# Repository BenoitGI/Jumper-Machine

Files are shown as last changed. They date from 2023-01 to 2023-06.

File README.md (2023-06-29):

 <h1> Jumper Machine 2022/2023 </h1>

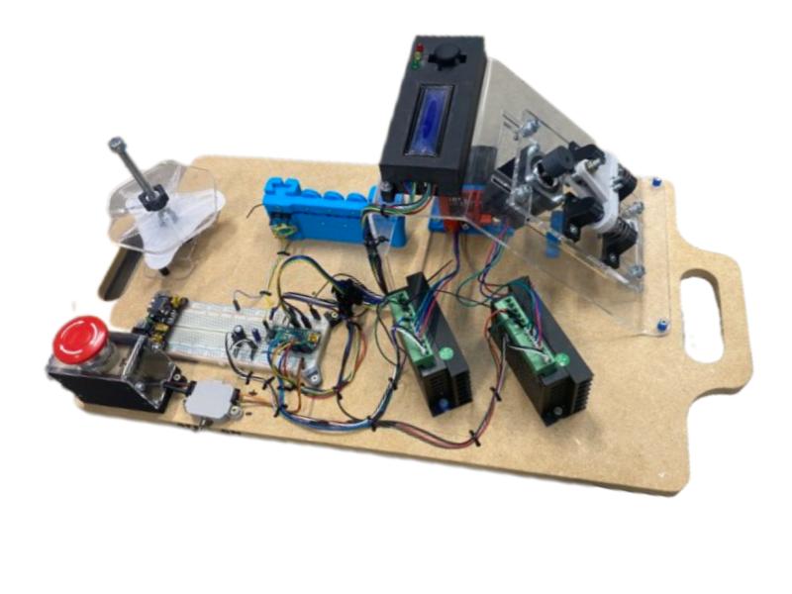
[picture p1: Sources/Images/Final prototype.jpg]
Jumper Machine final prototype


## Introduction
This OnShape project is a part of an french engineering school project (**Grenoble INP - Génie Industriel**) realized during 2022/2023. During 1 year, our group of 5 students had to make a machine prototype which would automatize the manufacturing of connecting wire for prototyping  named “jumper” from a wire reel. It was ordered by the **Ense3 Favlab** and realized on the **Smart Platform**.

We also own an OnShape file with all our CAD models and assemblies 
<center>

**[<span font-size:7em> Project's Onshape Link </span>](https://cad.onshape.com/documents/e23f2a9b7d5cbfc350862d24/w/3bd71b5e537bce5bc2623e5e/e/d0d5c7eefa7db94f148151a4)**

</center>

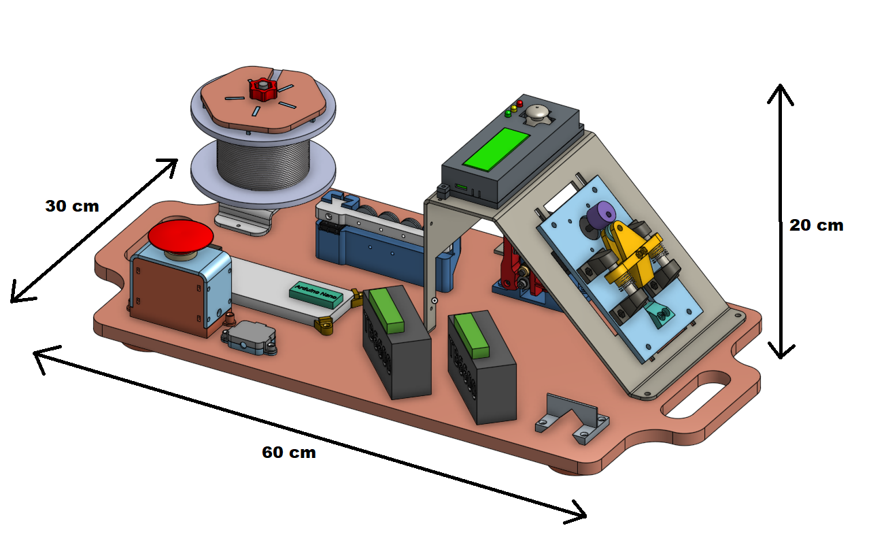
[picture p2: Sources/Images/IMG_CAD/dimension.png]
3D view with dimensions


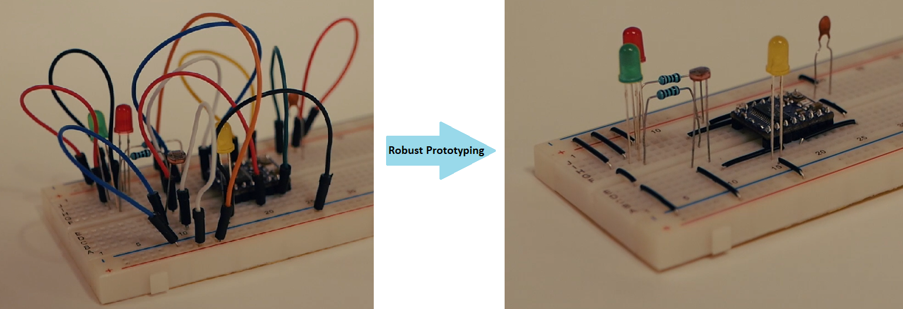
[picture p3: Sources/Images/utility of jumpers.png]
Utility of jumpers in prototyping


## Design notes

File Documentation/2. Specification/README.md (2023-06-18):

# **Specifications**

In order to best meet the customer's needs, we felt it was more efficient to ask him directly what he wanted from our machine. To do this, we drew up a first set of specifications and sent them to him. This was followed by several email exchanges and corrections to the specifications. We were also able to prioritize the functions of the machine from the most important to the least important with the customer. We also integrated a method of verification for each function (visual method, on software, by measurement, etc). To date, here are our main objectives.

## **Main objectives of this project**
<details>
  <summary>Jumper machine : objectives and constraints</summary>

First of all, the machine must distribute rigid wire. It must therefore be fed with wire, tension the wire and make it circulate in the system. The tensioned wire must not deviate from its initial axis by more than 1 millimeter.

Then, the machine must cut the wire to the right length and in bizot (45 degree angle). The length of wire to be cut ranges from 5.08 to 50.8 mm with a pitch of 2.54 mm with a tolerance of 0.5 mm.

As for the removal of the sleeve, it must be done on the left and right parts of the cut wire on a length of 6.5 mm on each side with a tolerance of 0.5 mm. This step must be done with care in order not to damage the conductors. We have also thought of a sorting system in order to differentiate between the waste of the sleeve and the waste of the conductor wire.

For the bending part of the machine, the edges of the wires must be bent at 90° with a tolerance of 5°, and above all they must not modify the initial geometry of the wire, that is to say that the wire must remain straight.

Then, for the operation of the machine, the customer would like it to be powered by different sources (nomadic mode, 12v DC) and to withstand the temperature conditions of a laboratory. Moreover, the machine must also respect a rate of 1 jumper in 10 seconds. It must be reliable, i.e. it must produce at least 10 jumpers in a row that comply with the specifications mentioned above. But the machine must also be dismountable and mountable with simple tools in one hour maximum.

As far as safety is concerned, the customer would like the machine to stop completely in less than one second with a simple manipulation. Also, if the instructions are not followed, the machine should not start. Moreover, during its operation no moving part of the system should be reachable by the user.

Finally, for the spatial dimensions, the system must not exceed the dimensions L50*W30*H30 cm and must not weigh more than 15 Kg.
 </details>
 
## **State of the art**
<details>
  <summary>Cutting, stripping and dispensing wire</summary>

Since a few decades, human beings have been using wires, especially jumpers, for electronic systems and often need to cut and strip them. That’s why they have created both wire cutter and wire stipper, then he wanted to do both those tasks with only one tool. Today, there are machines which can automatically cut and strip wires. They can either be big industrial machines or homemade ones depending on making rate, quantity, … It’s also possible for some machines to bend wires in order to make jumpers.

Using wire stipper or special blades can be considered as the main way to get stripped wires even though a carbon-dioxide laser is a good solution as well. However, a carbon-dioxide laser is very expensive thus outside the budget. The last solution to strip a wire we thought about consisted in using chemicals to dissolve the wire sleeve but we have quickly forgotten this solution because of its dangerousness.

About bending, there are many existing solutions and not only the basic one by using a plier but also, for example, an interesting and uncommon way with a hot wire. On the Internet, most bending machines work with a spinning part (linked to a stepper) and an offset axis.
			
A wire cutting machine “typically feeds the wire in on a reel, marks the wire using an inkjet or hot stamp printing mechanism, cuts the wire, and then coils the finished product on another reel or stacks it in a guide channel” [2].
A wire cutting/stripping machine usually has a rotating blade that follows the input cable and strips or cuts away the insulation.
However, such tools are expensive, and can’t be afforded by small workshops. For example, the Model WS-212 wire stripping machine by Bluerock Tools costs $ 1,299.00. Moreover the machine weighs 90 kilograms which is not convenient to be carried. The main issue with old wire cutting machines is the fact that they are not accurate or reliable. They tend to waste material which is an important issue when you are doing a project for the school of the environment.

Before the appearance of the first machines for cutting and stripping electrical wires, these tasks had to be done manually. Thanks to the particular shape of its blades, the "classic" cutting pliers can easily cut wires of various diameters.

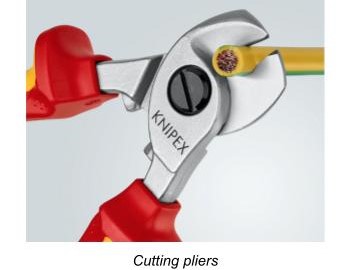
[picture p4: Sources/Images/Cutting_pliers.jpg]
Cutting pliers


For the stripping pliers, there are more or less sophisticated models. A calibrated wire stripper is very interesting for stripping small diameter wires, but its range of action is limited by its size. Indeed, the more it is possible to use it for different wires, the more it will be cumbersome. For this reason, it is sometimes interesting to have a second stripper at one's disposal to strip wires with a larger diameter.

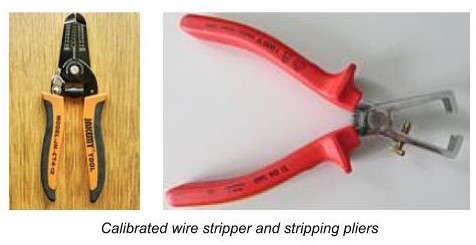
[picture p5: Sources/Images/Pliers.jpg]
Pliers


Stripping a wire is based on the principle of two blades that partially cut a sleeve that surrounds the electrical wires. Then pull to detach a piece of the sleeve. However, it may be interesting to be inspired by the principle of a foil cutter. That is to say, to have a device equipped with four rotating circular blades that can cut the sleeve around the wires completely.

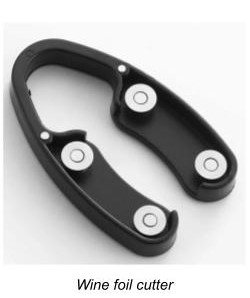
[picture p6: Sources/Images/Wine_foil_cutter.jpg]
Wine foil cutter


The use of blades to cut and strip wires is certainly the most common because of its simplicity, its low risk of injury but especially its very low cost compared to other devices. 

It is possible to perform these cutting and stripping tasks automatically with machines made by professionals [3] and usually sold at high prices. However, many individuals wish to have such machines to make their own jumpers. That's why there are DIY machines [4] with tutorials available online so you can make them yourself. All of these machines work in much the same way. The wire first passes through a tensioning system which also allows to straighten it. It’s then pulled by rollers which, according to their direction of rotation, make the wire advance or retreat. Finally, these machines use two V-shaped blades capable of cutting and stripping the wire. The whole thing is often managed by an Arduino type board that controls stepper motors. Finally, the use of such machines allows to cut and strip wires much faster than with pliers. It is especially possible to manufacture some of them for a lower cost.

V-blade technology is not the only technology that can be used for wire stripping. In fact, some individuals have already built their own machines and used a laser to strip the wires.

You might wonder why should a laser be considered for this purpose when the equipment is significantly more expensive than the competing methods?
The answer lies in its easy integration with electromechanical equipment, high controllability, non-contact process and no cutting force on the workpiece. Previous researches have proved that laser means has absolute advantages over traditional ways of mechanical wire stripping. [5]

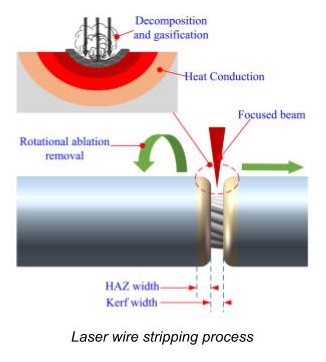
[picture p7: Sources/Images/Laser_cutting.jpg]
Laser stripping


Currently, carbon dioxide lasers are used on stripping machines because of their ability to selectively remove only the insulation without damaging the wire.
The absorption coefficient of non-metal material for this kind of laser wavelength is high and the absorption coefficient of metal material for this kind of laser wavelength is low, so the metal layer will not be damaged.
Laser wire stripping has been effectively applied as a production process in the aerospace, medical and data communications fields. There are specific advantages of using a laser over other methods but the emphasis varies from application to application.

Advantages : 
Selectively removes insulation with no conductor damage.
Near perfect process yield.
Lowest rework costs.
Provides excellent wire integrity, significantly increasing product life and reliability.
Can be automated, reducing labor costs.

Lasers have become valuable tools in manufacturing. Laser wire stripping is now performing production requirements very satisfactorily. The companies requiring wire stripping can now use lasers for this purpose and have various processes that cover all insulation materials presently in use.

Drawbacks :
High component costs.
If not fully automated, need for protection for users (closed carter and protective eyewear).
Need for a ventilation system to avoid accumulation of toxic fumes.

In the 2000s, NASA developed a manufacturing standard for wire stripping using chemical agents [6] . This method can only be used for single-conductor wires, but it is effective and allows a clean stripping without sleeve residues. However, the use of such chemical agents remains dangerous even if it seems to be possible to buy professional chemical pots [7] that enable the user to strip wires by using the method with chemical agents.

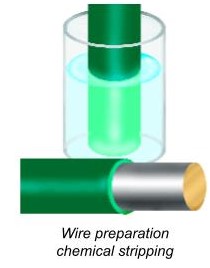
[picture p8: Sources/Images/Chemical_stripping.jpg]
Chemical stripping


In order to bend the wires in the least complex way possible, one would simply use pliers to bend the stripped ends into the desired jumper shape. The disadvantage of this method is that it is not very fast, it can be a pain for smaller wires and it does not allow a good regularity of the jumper shape. On the other hand, it is possible to consider 3D printing a bending die allowing to deposit the wires according to the corresponding size, then to press on the edges in order to bend them. This method could also be semi-automated or even totally automated by considering two dies (female and male) that would perform the bending and would overcome some of the shortcomings of the entirely manual method.

The most commonly used solution for bending wires is to use a part controlled by a stepper motor and equipped with an eccentric and extruded cylinder. There are many machines with different designs. Indeed, some are arranged horizontally [8] and others vertically [9] . It does not seem that either of these operating modes offers any particular advantages. The majority of the machines only allow folding. However, there are some machines that are able to perform all three tasks at once [10] .

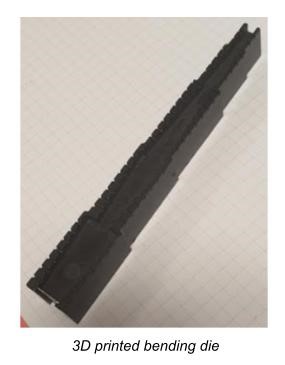
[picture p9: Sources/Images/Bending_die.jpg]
Bending die


The last possible method is probably one of the least used, but it is quite possible to bend wires using an electrically heated wire [11] . It works in much the same way as the bending die, but the effort required to bend the wire is reduced. The main disadvantage of this technique is obviously the risk of burning.

[2] Wire Cutting Machines Information, para. 1, Globalspec, accessed 06/10/2022, website, https://www.globalspec.com/learnmore/manufacturing_process_equipment/machine_tools/wire_cutting_machi nes 
[3]Eraser’s catalog, p.15-29, accessed 06/11/2022, pdf document, https://www.eraser.com/pdf/Eraser_Catalog.pdf
[4] Wire cutter stripper machine DIY, Ivan Rodyk, accessed 06/11/2022, Youtube video, https://www.youtube.com/watch?v=mNCjpKPapnc&ab_channel=IvanRodyk
[5] Study on the optimal process parameters for stripping the X-ETFE insulation layer of aviation wires by a small semiconductor laser, Sage Journals, accessed 10/10/2022, Research Article, https://doi.org/10.1177/16878132221127592
[6] Wire Preparation Chemical Stripping, Nasa Workmanship Standard, accessed 06/11/2022, Research Article, https://workmanship.nasa.gov/lib/insp/2%20books/links/sections/104%20Chemical%20Stripping.html
[7] Chemical Wire Stripping, Eraser, accessed 06/11/2022, Website, https://www.eraser.com/products/wire-cable-strippers/chemical-wire-stripping/
[8] DIY Wire Bender ets wires all bend into shape, Steven Dufresne, Hackaday, accessed 06/11/2022, Blog, https://hackaday.com/2018/10/14/diy-wire-bender-gets-wires-all-bent-into-shape/
[9] Arduino wire bender probably won’t kill all humans, Kristina Panos, Hackaday, accessed 06/11/2022, Blog, https://hackaday.com/2019/09/28/arduino-wire-bender-probably-wont-kill-all-humans/
[10] Fully Automatic Wire Cutter Stripper Bender Machine YH-680Z, Kunshan Yuanhan Electronic Equipment, accessed 06/11/2022, Youtube video, https://www.youtube.com/watch?v=nUAdrEDehpE&ab_channel=KunshanYuanhanElectronicEquipment
[11] Bending materials with a simple hot wire forming tool, Mike Szczys, Hackaday, accessed 06/11/2022, Blog, https://hackaday.com/2013/02/28/bending-materials-with-a-simple-hot-wire-forming-tool/
 </details>
	
## **Stakeholders**
<details>
  <summary>Stakeholders</summary>
	
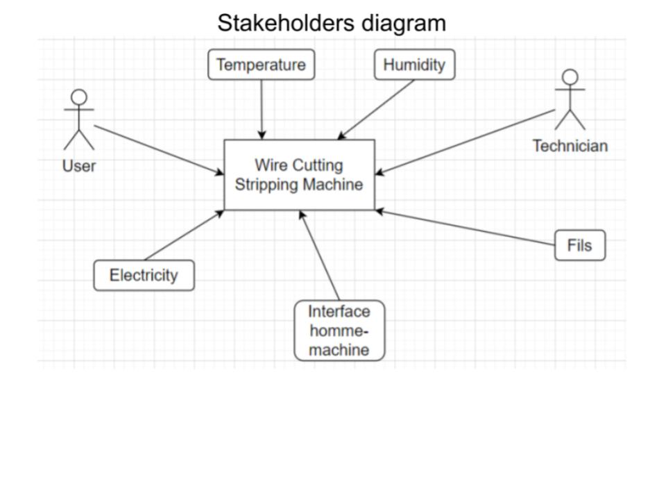
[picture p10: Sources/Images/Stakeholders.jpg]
Stakeholders of the jumper machine

	
 </details>

## **Requirement**

<details>
  <summary>Specifications</summary>

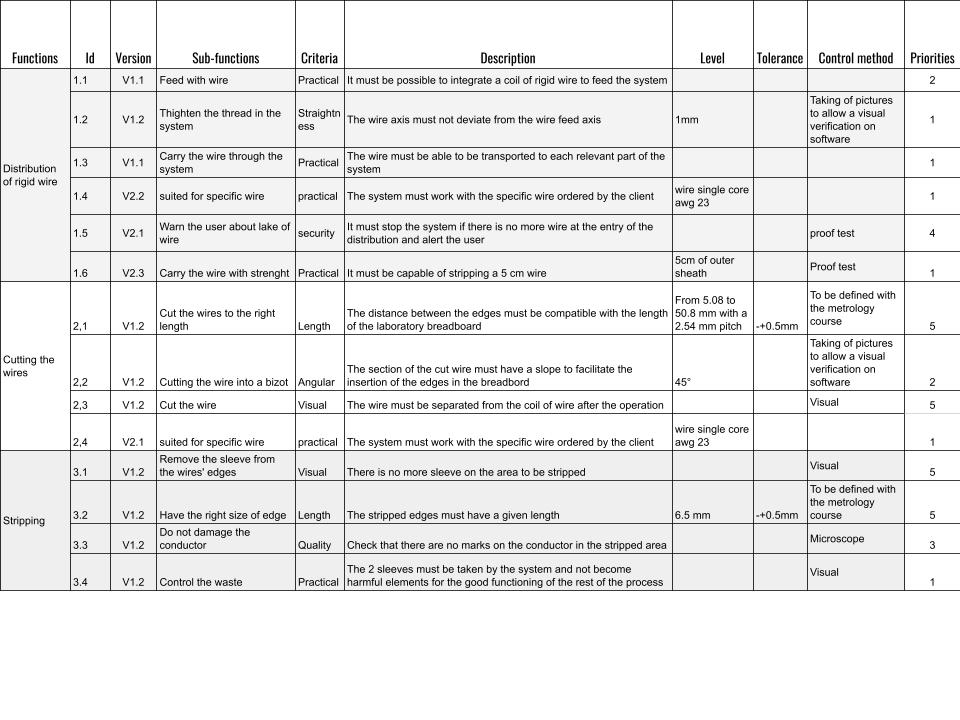
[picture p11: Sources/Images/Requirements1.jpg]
Requirements part 1

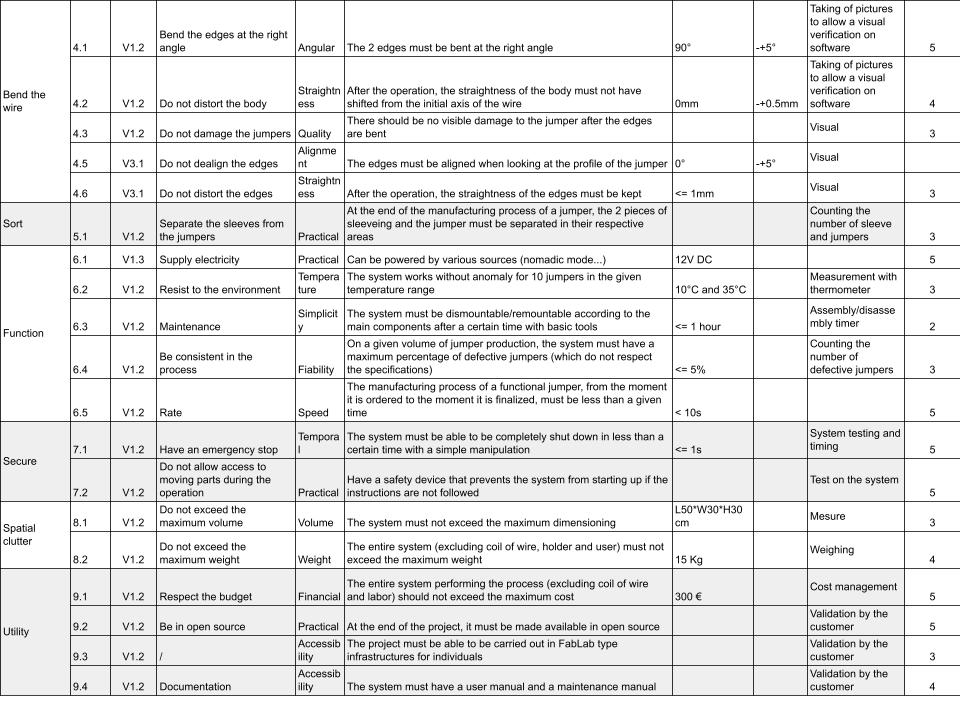
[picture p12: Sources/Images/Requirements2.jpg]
Requirements part 2


 </details>
 
## **Workplan**
<details>
  <summary>Project managment</summary>

  From the beginning of the project, we had in mind to share the work between us by "Functional Block" of the project (cut, strip, fold, feed) to allow us to advance in parallel and thus to be more efficient. Moreover, our objective was to get as close as possible to the customer's expectations by regularly exchanging with him on our progress or our questions.
That's why the AGILE method seemed to be adapted in our case.

We are going to apply it by separating ourselves into two groups (2 and 3 people) who will each take care of one of the functional blocks during a design cycle and which will then be concluded by a customer feedback. Once this feedback is done, we start a new design cycle, either to make adjustments or to start a new functional block.
Moreover, this method offers us the advantage of being quite flexible because if we are short of time, we can decide to "amputate" the system of certain functions (the priorities having been defined with the customer).

As things stand now, and taking into account that we don't only have the PDP in our schedule. We hope to complete at least 2 cycles before we reach the phase where we will integrate all our functional blocks into the complete system (assembly phase).

Agile cycle

Our goal is to send at least one email to the client every 2 weeks to allow him to be involved in our progress. 
For now, we have done all the preparatory phase to be able to divide the work and understand the ins and outs of the project. Now, we will split up and start the first Agile cycle in anticipation of a meeting with the client just before the Christmas vacations.

With regard to document management, we have a drive because the project is not subject to industrial confidentiality. And we have decided on a title nomenclature as follows:

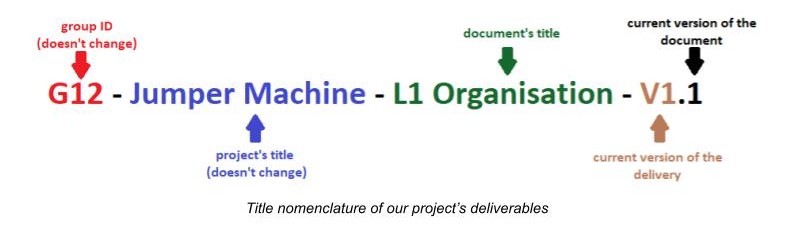
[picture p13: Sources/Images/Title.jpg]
Documents nomenclature
	

Nevertheless, we make sure that the latest version of a document is on chamilo.

</details>

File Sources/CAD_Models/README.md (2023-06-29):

You will find here all the **CAD models** used to build the Jumper Machine. 
we remind you that we have an OnShape repository (if you have a licence)  where their are all our CAD models and assemblies : 

[Jumper Machine 2022/2023](https://cad.onshape.com/documents/e23f2a9b7d5cbfc350862d24/w/3bd71b5e537bce5bc2623e5e/e/d0d5c7eefa7db94f148151a4)

For each of our part on this GitHub project,  you'll have :
- **.STL** if you just want to print the part.
- **.Dxf** if it's a part make by a laser cutting technologie.
- **.pdf** for bending plans for certain parts
- **.FCStd** which allow you to modify the part on a free and open-source CAD software named [**FreeCAD**](https://www.freecad.org/index.php).

# Jumper Machine Nomenclature
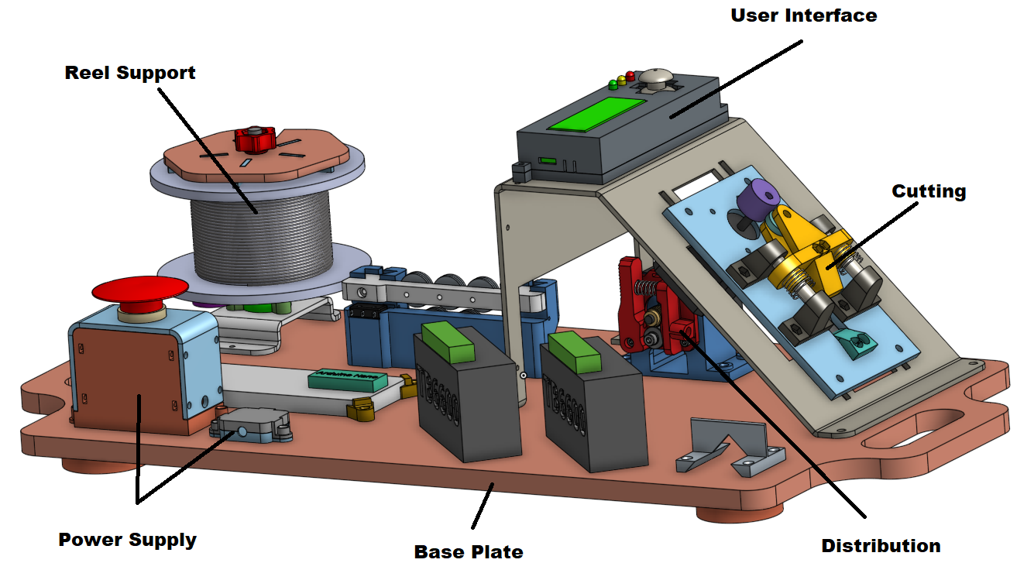
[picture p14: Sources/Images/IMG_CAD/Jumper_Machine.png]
Jumper Machine nomenclature


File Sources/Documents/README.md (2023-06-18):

Here you will find all our **pdf files** that can provide more information about this project. Most of these documents have been produced for school use.

# Deliverables
There are 4 deliverables which have been our milestones during the project.

- **Deliverable 1** : to present the project, our objectives and the state of the art.
- **Deliverable 2** : it explains our work around the _distribution and cutting system_.
- **Deliverable 4** : it explains our work around the _stripping and bending system_.
- **Final Deliverable** : It present our final prototype after an implemanting phase with all the previous sub-systems.

# Cost Analysis
It contains a **bill of materials** with links, the **labor cost** and the **process cost** of the project during this year.

# B.O.M
A specific pdf for the **bill of materials**if you don't want the rest of the cost analysis but just a shopping list.

# User Manual
It explain the very basics of how to start the machine.

# Maintenance Guide
It lists all the functional problems encountered during the project. It also contains suggestions for improving the machine.

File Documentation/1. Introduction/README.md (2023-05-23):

# Introduction

Final prototype

## Motivation

Our project focuses on a jumper cutting and stripping machine.
This machine should be used in schools (above all Ense3) for learning and research purposes.
Its main functions will be to cut jumpers for electrical devices such as breadboards and strip the jumpers out of their protective wire sleeve.

## Goals

The main purpose of this machine is to allow students and researchers to work faster.
Indeed, cutting jumpers, stripping them and bending them takes time.
According to the client, the main issue with doing these tasks by hand is the inaccuracies of the jumper’s length and the jumpers not being bent correctly.
Indeed, the corners of the jumper are usually not straight but curved toward its center. This curve makes it difficult to place the jumpers on the breadboard. 

So the first challenge is to straighten and harden the corners of the jumpers.
Then, the jumper’s length is also difficult to get right by hand.
If the jumper is too long it will bend or create knots with the other jumpers, whereas if it is too short, it won’t fit in the dedicated space.
Also when the jumper’s length is not right, the electrical contacts are not made or badly made.

## History

The project originated from a researcher, Frédéric Mantegazza.

## Documentation structure

- Introduction
- Specification
- Design 
- Manufacturing
- Assembly
- Use
- Maintenance
- Disposal

## Required skills

To reproduce or modify the cutting machine, it is necessary to know the basic mechanics as well as the electronics and coding related to the Arduino.
This product has been intentionnally designed to be manufactured in any fablab with cutting machines and 3D printers.

## Contribution Process

The machine will be delivered to the Ense3 FABLAB and will be tested currently under test by various people.
An improved version will certainly be welcome in a near future.
In any case you can contact: jean-francois.boujut@grenoble-inp.fr
Parts of this project (mostly cutting part) were inspired by the following project: https://github.com/TomGosnik/FairEmbo-Project

## Last updates 

23/05/2023

## Initial project team

"Benoit Veran" benoit.veran@grenoble-inp.org
"Virgile Marty" virgile.marty@grenoble-inp.org
"Bastien Vincent" bastien.vincent@grenoble-inp.org
"Florian Boulay" florian.boulay@hotmail.com
"Clara Heid" clara.heid@grenoble-inp.org

## Sponsors and Partners

Grenoble INP Génie Industriel : https://genie-industriel.grenoble-inp.fr/,
Grenoble INP Ense3 : https://ense3.grenoble-inp.fr/fr/l-ecole/fablab,
Plateforme Smart : https://s-mart.fr/

## Acknowledgements

Florian, Clara, Virgile, Benoît and Bastien would like to thank the teachers for their support throughout this project, as well as Mr. Mantegazza for his help during some difficult phases.

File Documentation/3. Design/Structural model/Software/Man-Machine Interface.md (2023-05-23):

## **Man-machine interface**

Creating a HMI was an important step to ensure the machine is usable. It allows the user to change the parameters of the machine without changing the code. Different menus were set up to change those values: for the number of jumpers to cut, for their length and for the positioning of the blade to strip the wire. Also two more menus were added: one to feed the wire once it’s in the extruder (avoiding a tedious task by hand) and the menu to start the program to make jumpers. A joystick can change menus vertically and change the values of the menus concerned horizontally, once entered with the button of this joystick. To see that information, a simple 16x2 screen was added for the precise information, and three LEDs were added: green when everything is functioning and it’s fine to manipulate the machine, orange when everything is functioning but one or both motors are functioning, and red when wire is missing.

 ### **1. Components**
<details>
  <summary>Descrition of the man machine interface</summary>
 
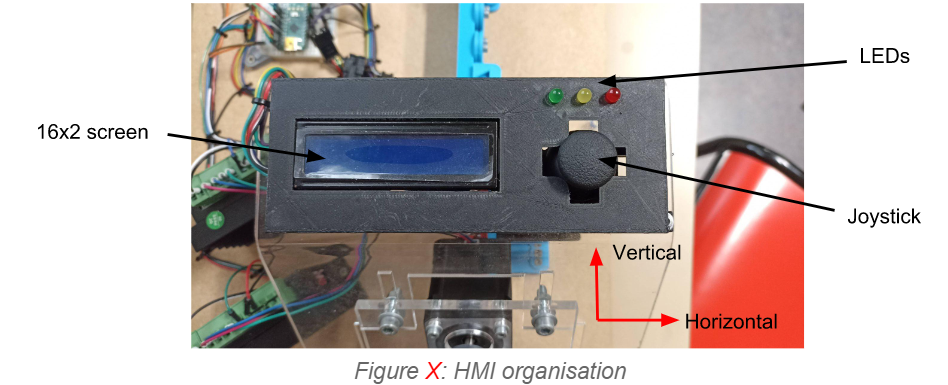
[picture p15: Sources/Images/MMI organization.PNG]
Man machine interface
 
 
 </details>
 
 ### **2. Algorithm and functionning**
<details>
  <summary>Click to see the guideline!</summary>
 
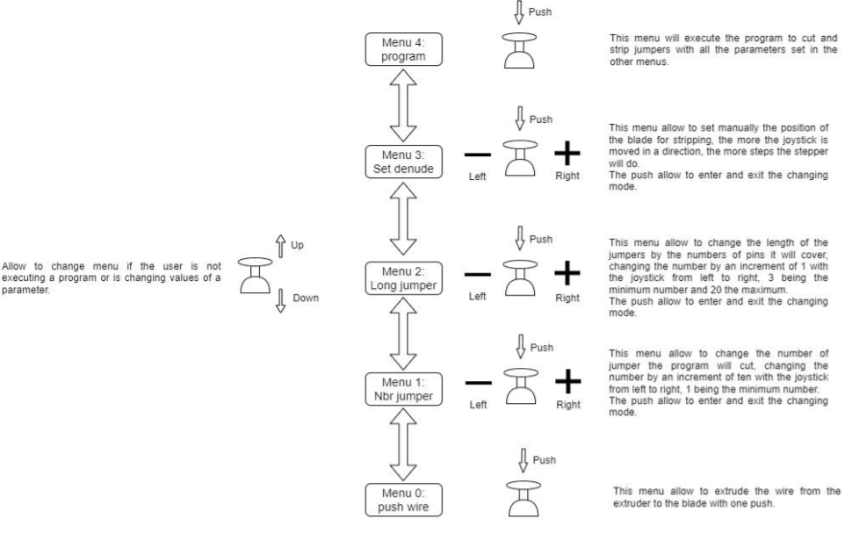
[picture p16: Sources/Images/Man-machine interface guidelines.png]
Man machine interface guidelines
 
</details>

<details>
 <summary>How to set the stripping position</summary>
 </br>
 When you enter the “set denude” menu, you will be able to set the blade to the position of stripping, where it is just cutting the sheath.
 
 The first step will be to ensure a small part of the wire is stepping out of the machine (it will be cut of when you run the program, so you don’t need to much wire because it’s waste).
 
 Then once you enter the menu, you can move the cam with the joystick in one way, the way it will cut during the program (you can turn back of course but it will be blocked at its original position to avoid to turn in way to strip and another way to cut during the program). The more you push the joystick on its side, the more the cam turns, to get close faster but position it more precisely. The screen is showing the number of steps the wire moved from the origin.
 
 Once you get the blades closer to the wire, move them until they can’t move anymore unless the cut the core of the wire. If you found the stripping position, you can press the joystick. You will leave the menu; the cam will turn back to its origin and the screen will show the position of stripping (in number of steps).
 
 It’s recommended to run the program with only one jumper at the time of the desired length to check it’s working, and repeat it once or twice. If it’s not working, change the position of stripping (bigger from the previous position if not cutting enough the sheath, smaller than the previous position if cutting too much and biting into the core).
 
 If it’s working well, you can run the program with the desired number of jumpers.

</details>

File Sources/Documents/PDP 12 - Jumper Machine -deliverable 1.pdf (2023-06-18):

LIVRABLE 1 : JUMPER CUTTING/STRIPPING MACHINE

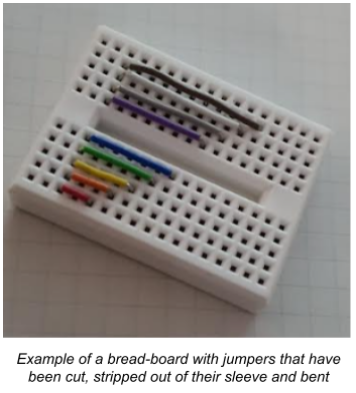
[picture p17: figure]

Date : 8/11/2022

Groupe N° : 12

Names : Boulay Florian - Heid Clara - Marty Virgile - Véran Benoît - Vincent Bastien

Collaborative Design Project

# Content

Livrable 1 : Jumper cutting/stripping machine | 1
1. Context of the study | 3
2. Problem statement | 4
3. Main objective of the project | 4
4. Delivery | 6
5. State of the art | 6
6. Workplan | 12
Bibliography | 14

1. CONTEXT OF THE STUDY

Our project focuses on a jumper cutting and stripping machine, ordered by Frédéric Mantegazza. This machine should be used in schools (above all Ense3) for learning and research purposes. Its main functions will be to cut jumpers for electrical devices such as breadboards and strip the jumpers out of their protective wire sleeve.

The people who will interact with the machine will mostly be students and professors. They will also be the ones to repair the machine if it ever gets broken. Indeed, our client wants us to create a maintenance and instructions manual. Also, users should be able to interact with the machine through an interface to give the machine clear instructions. The machine won’t have to be sustainable in a harsh environment, however it must handle temperatures between 0°C and 30°C. The machine also has to interact with the jumpers : it must roll them out of the coil of wire, stretch them, cut them, strip them and bend them. In order to do so, the machine will be powered by a battery or an external power supply.

For this project, we have a maximum budget of 300 euros. Considering that we have many pieces to buy, this is a tight budget. We must indeed buy blades to cut the jumpers, tensioning rollers to keep the jumpers still, and maybe cutting pliers. We might also have to buy raw material such as plexiglass boards or wooden boards to build the housing of the machine. The other devices such as motors and the Arduino card should be found in GINOVA.

It is important to know that such machines already exist on the market. They are extremely performant : they do all the mentioned functions : cutting, stripping and bending the wire, and they do it neatly and fastly. The only issue is that they are expensive : for instance,the cheapest models for strip and cut wire cost around 800 € [1].

2. PROBLEM STATEMENT

The main purpose of this machine is to allow students and researchers to work faster. Indeed, cutting jumpers, stripping them and bending them takes time. According to the client, the main issue with doing these tasks by hand is the inaccuracies of the jumper’s length and the jumpers not being bent correctly. Indeed, the corners of the jumper are usually not straight but curved toward its center. This curve makes it difficult to place the jumpers on the breadboard.

So the first challenge is to straighten and harden the corners of the jumpers. Then, the jumper’s length is also difficult to get right by hand. If the jumper is too long it will bend or create knots with the other jumpers, whereas if it is too short, it won’t fit in the dedicated space. Also when the jumper’s length is not right, the electrical contacts are not made or badly made.

3. MAIN OBJECTIVE OF THE PROJECT

In order to best meet the customer's needs, we felt it was more efficient to ask him directly what he wanted from our machine. To do this, we drew up a first set of specifications and sent them to him. This was followed by several email exchanges and corrections to the specifications. We were also able to prioritize the functions of the machine from the most important to the least important with the customer. We also integrated a method of verification for each function (visual method, on software, by measurement, etc). To date, here are our main objectives.

First of all, the machine must distribute rigid wire. It must therefore be fed with wire, tension the wire and make it circulate in the system. The tensioned wire must not deviate from its initial axis by more than 1 millimeter.

Then, the machine must cut the wire to the right length and in bizot (45 degree angle). The length of wire to be cut ranges from 5.08 to 50.8 mm with a pitch of 2.54 mm with a tolerance of 0.5 mm. Here is the nomenclature of a jumper to make it clearer :

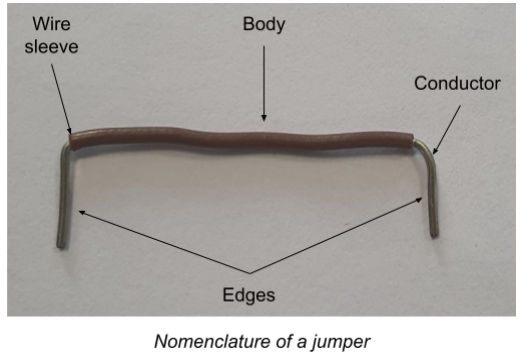
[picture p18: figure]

As for the removal of the sleeve, it must be done on the left and right parts of the cut wire on a length of 6.5 mm on each side with a tolerance of 0.5 mm. This step must be done with care in order not to damage the conductors. We have also thought of a sorting system in order to differentiate between the waste of the sleeve and the waste of the conductor wire.

For the bending part of the machine, the edges of the wires must be bent at 90° with a tolerance of 5°, and above all they must not modify the initial geometry of the wire, that is to say that the wire must remain straight.

Then, for the operation of the machine, the customer would like it to be powered by different sources (nomadic mode, 12v DC) and to withstand the temperature conditions of a laboratory. Moreover, the machine must also respect a rate of 1 jumper in 10 seconds. It must be reliable, i.e. it must produce at least 10 jumpers in a row that comply with the specifications mentioned above. But the machine must also be dismountable and mountable with simple tools in one hour maximum.

As far as safety is concerned, the customer would like the machine to stop completely in less than one second with a simple manipulation. Also, if the instructions are not followed, the machine should not start. Moreover, during its operation no moving part of the system should be reachable by the user.

Finally, for the spatial dimensions, the system must not exceed the dimensions L50*W30*H30 cm and must not weigh more than 15 Kg.

4. DELIVERY

The Client expects us to create a working prototype that, at a minimum, would validate the functionality of such a system. The project started this year with our group, so we don't have any bedrock. The client plans to keep the project going (at least for the next year), so our work will be the bedrock for the next groups that will take over. The client doesn’t expect us to have a complete functional system. He asked us to prioritize the cutting and stripping of the wire with a minimum of electronic automation. The bending part can be done by a manual device for this year, but should also be automated in the long run.

Moreover, the project will have to be open source at the end, so it will be necessary to keep a clear documentation of what has been achieved to make it reproducible and improvable by people outside the project. A user manual and a maintenance manual are also expected at the end of our project.

The client has no particular expectations regarding the project's promotional video, so it will be made to meet the school's requirements.

5. STATE OF THE ART

Since a few decades, human beings have been using wires, especially jumpers, for electronic systems and often need to cut and strip them. That’s why they have created both wire cutter and wire stipper, then he wanted to do both those tasks with only one tool. Today, there are machines which can automatically cut and strip wires. They can either be big industrial machines or homemade ones depending on making rate, quantity, … It’s also possible for some machines to bend wires in order to make jumpers.

Using wire stipper or special blades can be considered as the main way to get stripped wires even though a carbon-dioxide laser is a good solution as well. However, a carbon-dioxide laser is very expensive thus outside the budget. The last solution to strip a wire we thought about consisted in using chemicals to dissolve the wire sleeve but we have quickly forgotten this solution because of its dangerousness.

About bending, there are many existing solutions and not only the basic one by using a plier but also, for example, an interesting and uncommon way with a hot wire. On the Internet, most bending machines work with a spinning part (linked to a stepper) and an offset axis.

A wire cutting machine “typically feeds the wire in on a reel, marks the wire using an inkjet or hot stamp printing mechanism, cuts the wire, and then coils the finished product on another reel or stacks it in a guide channel” [2].

A wire cutting/stripping machine usually has a rotating blade that follows the input cable and strips or cuts away the insulation.

However, such tools are expensive, and can’t be afforded by small workshops. For example, the Model WS-212 wire stripping machine by Bluerock Tools costs $ 1,299.00. Moreover the machine weighs 90 kilograms which is not convenient to be carried. The main issue with old wire cutting machines is the fact that they are not accurate or reliable. They tend to waste material which is an important issue when you are doing a project for the school of the environment.

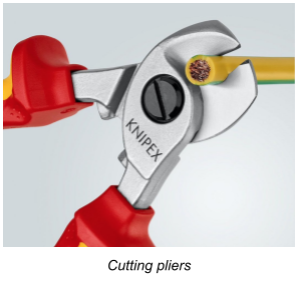
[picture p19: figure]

Before the appearance of the first
machines for cutting and stripping electrical wires, these tasks had to be done manually. Thanks to the particular shape of its blades, the "classic" cutting pliers can easily cut wires of various diameters.

For the stripping pliers, there are more or less sophisticated models. A calibrated wire stripper is very interesting for stripping small diameter wires, but its range of action is limited by its size. Indeed, the more it is possible to use it for different wires, the more it will be cumbersome. For this reason, it is sometimes interesting to have a second stripper at one's disposal to strip wires with a larger diameter.

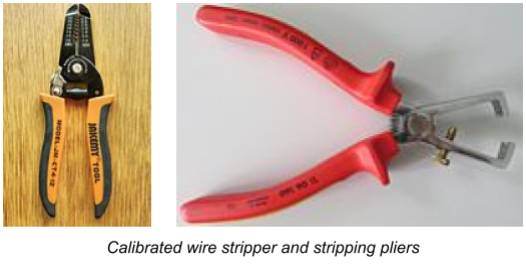
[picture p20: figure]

Stripping a wire is based on the principle of two blades that partially cut a sleeve that surrounds the electrical wires. Then pull to detach a piece of the sleeve. However, it may be interesting to be inspired by the principle of a foil cutter. That is to say, to have a device equipped with four rotating circular blades that can cut the sleeve around the wires completely.

The use of blades to cut and strip wires is certainly the most common because of its simplicity, its low risk of injury but especially its very low cost
compared to other devices.

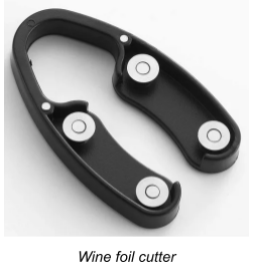
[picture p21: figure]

It is possible to perform these cutting and stripping tasks automatically with machines made by professionals [3] and usually sold at high prices. However, many individuals wish to have such machines to make their own jumpers. That's why there are DIY machines [4] with tutorials available online so you can make them yourself. All of these machines work in much the same way. The wire first passes through a tensioning system which also allows to straighten it. It’s then pulled by rollers which, according to their direction of rotation, make the wire advance or retreat. Finally, these machines use two V-shaped blades capable of cutting and stripping the wire. The whole thing is often managed by an Arduino type board that controls stepper motors. Finally, the use of such machines allows to cut and strip wires much faster than with pliers. It is especially possible to manufacture some of them for a lower cost.

V-blade technology is not the only technology that can be used for wire stripping. In fact, some individuals have already built their own machines and used a laser to strip the wires.

You might wonder why should a laser be considered for this purpose when the equipment is significantly more expensive than the competing methods?
The answer lies in its easy integration with electromechanical equipment, high controllability, non-contact process and no cutting force on the workpiece. Previous researches have proved that laser means has absolute advantages over traditional ways of mechanical wire stripping. [5]

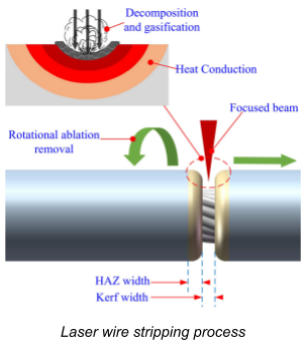
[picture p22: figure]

Currently, carbon dioxide lasers are used on stripping machines because of their ability to selectively remove only the insulation without damaging the wire.
The absorption coefficient of non-metal material for this kind of laser wavelength is high and the absorption coefficient of metal material for this kind of laser wavelength is low, so the metal layer will not be damaged.

Laser wire stripping has been effectively applied as a production process in the aerospace, medical and data communications fields. There are specific advantages of using a laser over other methods but the emphasis varies from application to application.

Advantages :
- Selectively removes insulation with no conductor damage.
- Near perfect process yield.
- Lowest rework costs.
- Provides excellent wire integrity, significantly increasing product life and reliability.
- Can be automated, reducing labor costs.

Lasers have become valuable tools in manufacturing. Laser wire stripping is now performing production requirements very satisfactorily. The companies requiring wire stripping can now use lasers for this purpose and have various processes that cover all insulation materials presently in use.

Drawbacks :
- High component costs.
- If not fully automated, need for protection for users (closed carter and protective eyewear).
- Need for a ventilation system to avoid accumulation of toxic fumes.

In the 2000s, NASA developed a manufacturing standard for wire stripping using chemical agents [6] . This method can only be used for single-conductor wires, but it is effective and allows a clean stripping without sleeve residues. However, the use of such chemical agents remains dangerous even if it seems to be possible to buy professional chemical pots [7] that enable the user to strip wires by using the method with chemical agents.

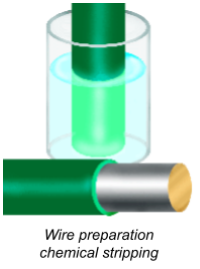
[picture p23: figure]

In order to bend the wires in the least complex way possible, one would simply use pliers to bend the stripped ends into the desired jumper shape. The disadvantage of this method is that it is not very fast, it can be a pain for smaller wires and it does not allow a good regularity of the jumper shape. On the other hand, it is possible to consider 3D printing a bending die allowing to deposit the wires according to the corresponding size, then to press on the edges in order to bend them. This method could also be semi-automated or even totally automated by considering two dies (female and male) that would perform the bending and would overcome some of the shortcomings of the entirely manual method.

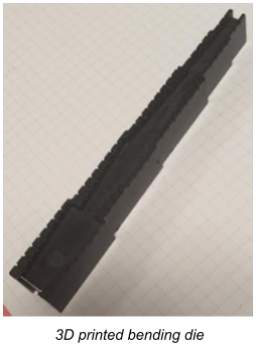
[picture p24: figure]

The most commonly used solution for bending wires is to use a part controlled by a stepper motor and equipped with an eccentric and extruded cylinder. There are many machines with different designs. Indeed, some are arranged horizontally [8] and others vertically [9] . It does not seem that either of these operating modes offers any particular advantages. The majority of the machines only allow folding. However, there are some machines that are able to perform all three tasks at once [10] .

The last possible method is probably one of the least used, but it is quite possible to bend wires using an electrically heated wire [11] . It works in much the same way as the bending die, but the effort required to bend the wire is reduced. The main disadvantage of this technique is obviously the risk of burning.

6. WORKPLAN

From the beginning of the project, we had in mind to share the work between us by "Functional Block" of the project (cut, strip, fold, feed) to allow us to advance in parallel and thus to be more efficient. Moreover, our objective was to get as close as possible to the customer's expectations by regularly exchanging with him on our progress or our questions. That's why the AGILE method seemed to be adapted in our case.

We are going to apply it by separating ourselves into two groups (2 and 3 people) who will each take care of one of the functional blocks during a design cycle and which will then be concluded by a customer feedback. Once this feedback is done, we start a new design cycle, either to make adjustments or to start a new functional block.
Moreover, this method offers us the advantage of being quite flexible because if we are short of time, we can decide to "amputate" the system of certain functions (the priorities having been defined with the customer).

As things stand now, and taking into account that we don't only have the PDP in our schedule. We hope to complete at least 2 cycles before we reach the phase where we will integrate all our functional blocks into the complete system (assembly phase).

Our goal is to send at least one email to the client every 2 weeks to allow him to be involved in our progress.
For now, we have done all the preparatory phase to be able to divide the work and understand the ins and outs of the project. Now, we will split up and start the first Agile cycle in anticipation of a meeting with the client just before the Christmas vacations.

With regard to document management, we have a drive because the project is not subject to industrial confidentiality. And we have decided on a title nomenclature as follows:

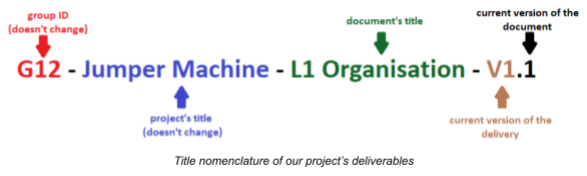
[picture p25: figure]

Nevertheless, we make sure that the latest version of a document is on chamilo.

BIBLIOGRAPHY

[1] Machine à Dénuder électrique, Vevor, accessed 06/10/2022, online shop, https://www.google.fr/aclk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 (https://www.google.fr/aclk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)
[2] Wire Cutting Machines Information, para. 1, Globalspec, accessed 06/10/2022, website, https://www.globalspec.com/learnmore/manufacturing_process_equipment/machine_tools/wire_cutting_machi nes (https://www.globalspec.com/learnmore/manufacturing_process_equipment/machine_tools/wire_cutting_machi)

[3]Eraser’s catalog, p.15-29, accessed 06/11/2022, pdf document, https://www.eraser.com/pdf/Eraser_Catalog.pdf

[4] Wire cutter stripper machine DIY, Ivan Rodyk, accessed 06/11/2022, Youtube video, https://www.youtube.com/watch?v=mNCjpKPapnc&ab_channel=IvanRodyk
[5] Study on the optimal process parameters for stripping the X-ETFE insulation layer of aviation wires by a small semiconductor laser, Sage Journals, accessed 10/10/2022, Research Article, https://doi.org/10.1177/16878132221127592
[6] Wire Preparation Chemical Stripping, Nasa Workmanship Standard, accessed 06/11/2022, Research Article,
https://workmanship.nasa.gov/lib/insp/2%20books/links/sections/104%20Chemical%20Stripp ing.html (https://workmanship.nasa.gov/lib/insp/2%20books/links/sections/104%20Chemical%20Stripping.html)
[7] Chemical Wire Stripping, Eraser, accessed 06/11/2022, Website, https://www.eraser.com/products/wire-cable-strippers/chemical-wire-stripping/
[8] DIY Wire Bender ets wires all bend into shape, Steven Dufresne, Hackaday, accessed 06/11/2022, Blog,
https://hackaday.com/2018/10/14/diy-wire-bender-gets-wires-all-bent-into-shape/
[9] Arduino wire bender probably won’t kill all humans, Kristina Panos, Hackaday, accessed 06/11/2022, Blog,
https://hackaday.com/2019/09/28/arduino-wire-bender-probably-wont-kill-all-humans/
[10] Fully Automatic Wire Cutter Stripper Bender Machine YH-680Z, Kunshan Yuanhan Electronic Equipment, accessed 06/11/2022, Youtube video, https://www.youtube.com/watch?v=nUAdrEDehpE&ab_channel=KunshanYuanhanElectronic Equipment (https://www.youtube.com/watch?v=nUAdrEDehpE&ab_channel=KunshanYuanhanElectronicEquipment)
[11] Bending materials with a simple hot wire forming tool, Mike Szczys, Hackaday, accessed 06/11/2022, Blog,
https://hackaday.com/2013/02/28/bending-materials-with-a-simple-hot-wire-forming-tool/

Picture’s link :

- cutting pliers (https://www.installation-renovation-electrique.com/wp-content/uploads/2017/05/avis-test-pince-coupe-cable-knipex-9516165-1068x900.jpg)
- calibrated wire stripper (https://upload.wikimedia.org/wikipedia/commons/thumb/a/a5/Tool_1530843.jpg/800px-Tool_1530843.jpg)
- stripping pliers (https://upload.wikimedia.org/wikipedia/commons/thumb/e/e6/Abisolierzange.jpg/1280px-Abisolierzange.jpg)
- wine foil cutter (https://5.imimg.com/data5/SELLER/Default/2020/9/KI/UL/VA/8842118/2-pack-magnetic-design-wine-foil-cutter-wine-bottle-opener-accessory-gift-for-wine-lovers-500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)
- wire preparation chemical stripping (https://workmanship.nasa.gov/lib/insp/2%20books/links/sections/graphics/104/104-01.gif)

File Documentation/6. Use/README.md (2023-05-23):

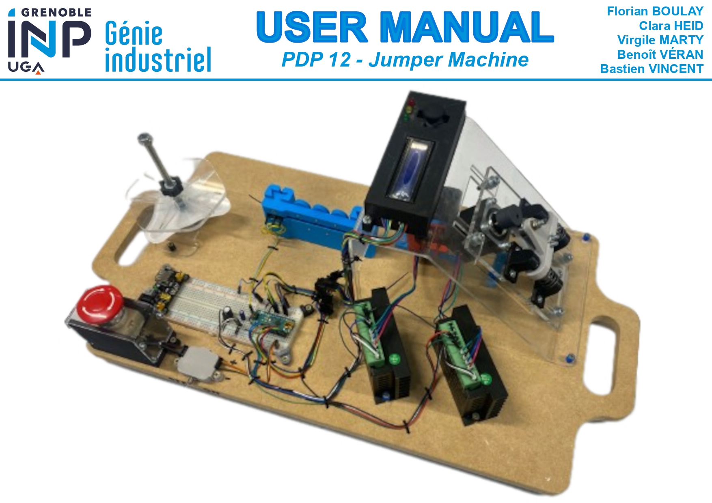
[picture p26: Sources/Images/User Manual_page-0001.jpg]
User Manual

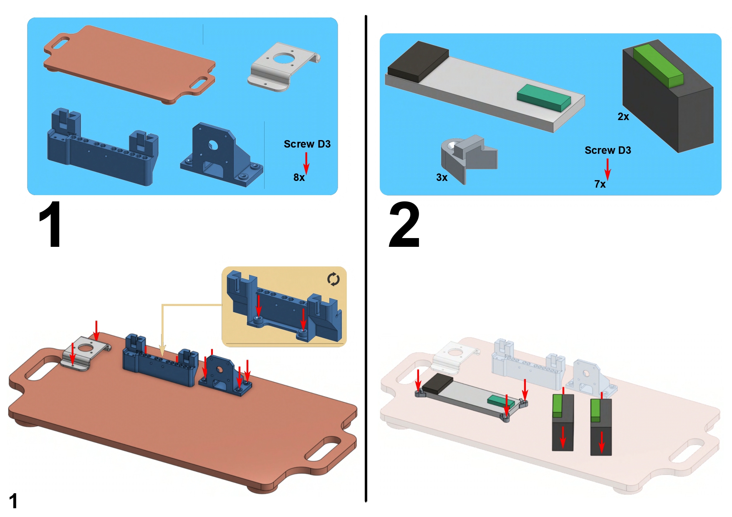
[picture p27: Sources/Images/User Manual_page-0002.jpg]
User Manual

User Manual
User Manual

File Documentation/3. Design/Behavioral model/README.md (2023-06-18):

# **Behavioral model**

Operating mode of the machine

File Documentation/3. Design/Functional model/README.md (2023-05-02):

We've chosen to divide the machine in two parts: the cutting and the distribution

# **Cutting and stripping**

<details>
  <summary>Function analysis</summary>

Cutting Function analysis

</details>

<details>
  <summary>Logical architecture</summary>

Cutting Logical Architecture

</details>

<details>
  <summary>System architecture</summary>

Cutting System Architecture

</details>
 
# **Distribution**

<details>
  <summary>Function analysis</summary>

Distribution Function analysis

</details>

<details>
  <summary>Logical architecture</summary>

Distribution Logical Architecture

 </details>
 
 <details>
  <summary>System architecture</summary>

Distribution System Architecture

</details>

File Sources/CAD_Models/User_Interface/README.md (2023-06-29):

# User Interface nomenclature
UI nomenclature

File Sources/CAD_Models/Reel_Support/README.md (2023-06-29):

# Reel Support nomenclature
reel support nomenclature

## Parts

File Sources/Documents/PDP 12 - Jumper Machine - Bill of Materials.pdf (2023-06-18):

# Bill of materials (B.O.M.)

Component | Unit Price (euros) TTC | Quantity | Supplier | Step | Comments | Order URL
V blade | 7,37 € | 1 | AliExpress | Agile 1 - Cutting | 38*16*30 | Lâminas de reposição peças lâmina de faca (https://pt.aliexpress.com/item/1005004654673651.html?curPageLogUid=zdUZEhKgOndx) de aço para swt508c swt508e fio descascando peeling máquina de corte| | - AliExpress
Stepper motor Nema 17 | 19,50 € | 2 | Go Tronic | Agile 1 - Cutting & Distribution | 59 Ncm 2A | https://www.gotronic.fr/art-moteur-17hs19-2004s-18355.htm
Drivers TB6600 | 20,95 € | 2 | Go Tronic | Agile 2 - Cutting & distrib | more efficient than the A8850 | https://www.gotronic.fr/art-commande-moteur-pas-a-pas-dri0043-25551.htm
Arduino Nano | 25,90 € | 1 | Go Tronic | All | https://www.gotronic.fr/art-arduino-nano-12422.htm
Breadboard kit with power supply | 9,50 € | 1 | Go Tronic | All | includes jumpers and a 5 V power supply | https://www.gotronic.fr/art-kit-plaque-de-montage-sd80a-25864.htm
ender 3 extruder | 13,49 € | 1 | Amazon | Agile 1 - Distribution
Limit switch | 0,86 € | 1 | L3D Service | Agile 1 - Distribution | Our current model have the little roll https://imprimante-3d-service.com/449-lot-de-5-interrupteurs-fin-de-course.html
Capacitor découplage 100µF | 0,07 € | 1 | Conrad | Agile 1 - Distribution
Tube Polyamide Legris 4mm*2,7mm | 17,95 € | 1 | RS | Agile 2 - Stripping | Need only 15 cm | https://fr.rs-online.com/web/p/tuyaux-a-air-comprime/0225218
Alimentation GS6012 Mean Well | 27,70 € | 1 | Go Tronic | Agile 3 | 12VDC ; 5A | https://www.gotronic.fr/art-adaptateur-gs6012-19953.htm
Emergency button | 7,80 € | 1 | Go Tronic | All | suited for the aliementation | https://www.gotronic.fr/art-bouton-d-arret-d-urgence-y090-19400.htm
Module joystick GT1079 | 2,90 € | 1 | Go Tronic | Agile 2 - Stripping | with the push button optionhttps://www.gotronic.fr/art-module-joystick-gt1079-26129.htm
LCD Arduino 16*2 I2C protocol | 8,50 € | 1 | Go Tronic | Agile - stripping | less pins used than without protocol | https://www.gotronic.fr/art-afficheur-lcd-i2c-2x16-caracteres-25650.htm
Connector USB A into mini USB b | 1,90 € | 1 | Go Tronic | Agile 2 | 1 m | https://www.gotronic.fr/art-cordon-1m-usb161-15307.htm
Cordon IEC155 | 6,90 € | 1 | Go Tronic | Agile 3 | 2 m | https://www.gotronic.fr/art-cordon-iec155-5013.htm
Total cost | 211,74 €

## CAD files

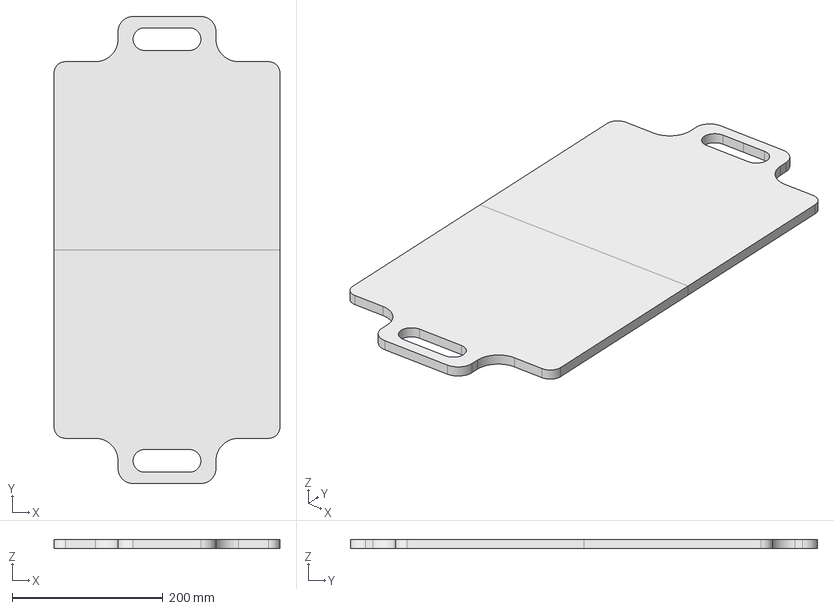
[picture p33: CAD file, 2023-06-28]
Sources/CAD_Models/Base_Plate/Base_Plate/Base_Plate.FCStd
300.0 x 620.0 x 12.0 mm

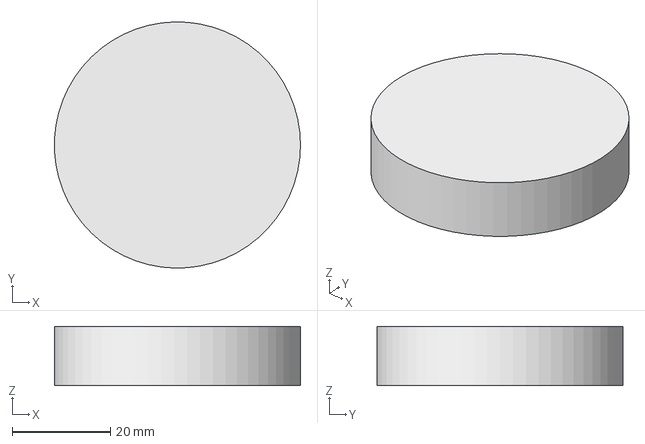
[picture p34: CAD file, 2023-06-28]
Sources/CAD_Models/Base_Plate/Base_Plate_Legs/Base_Plate_Legs.FCStd
50.0 x 50.0 x 12.0 mm

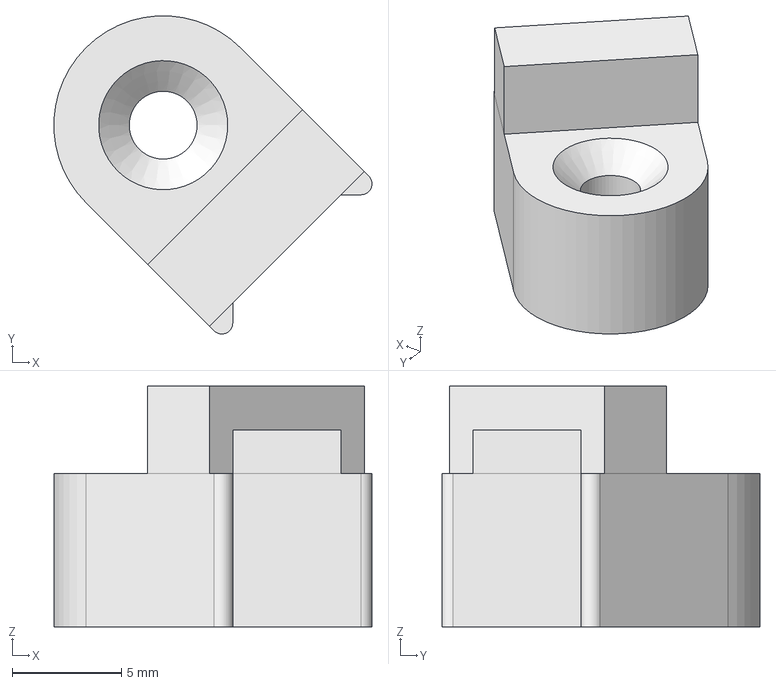
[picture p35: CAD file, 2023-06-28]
Sources/CAD_Models/Base_Plate/Breadboard_Corner_Anchor/Breadboard_Corner_Anchor.FCStd
14.5 x 14.5 x 11.0 mm

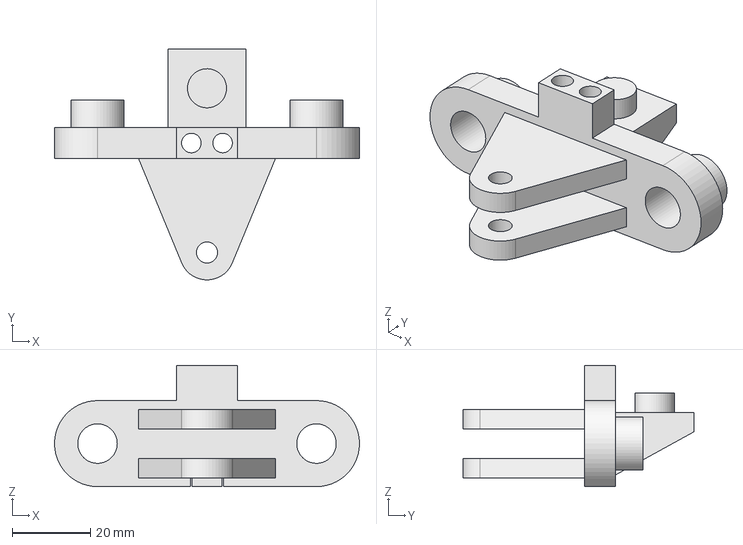
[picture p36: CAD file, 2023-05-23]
Sources/CAD_Models/Cutting/Blade_Holder/Blade_holder.FCStd
78.0 x 59.0 x 31.0 mm

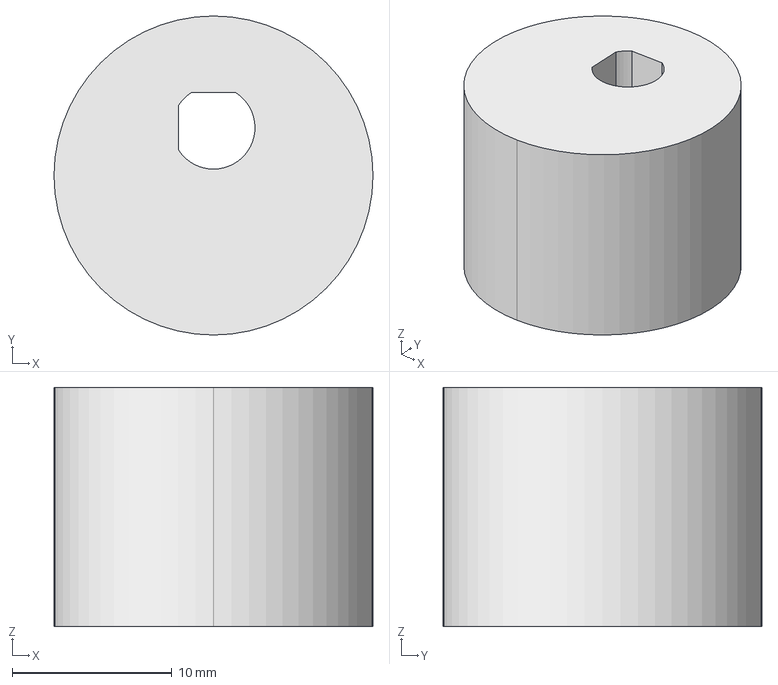
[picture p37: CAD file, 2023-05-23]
Sources/CAD_Models/Cutting/Cam/came.FCStd
20.0 x 20.0 x 15.0 mm

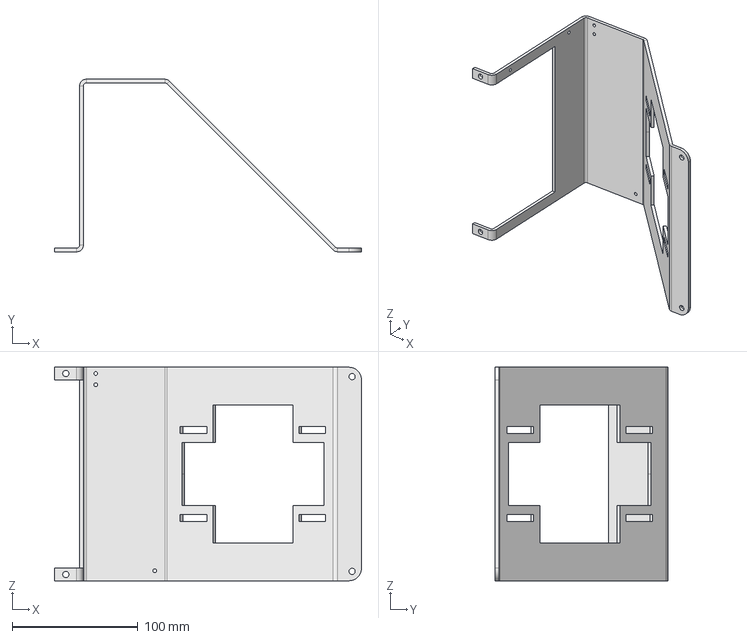
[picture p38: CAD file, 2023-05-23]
Sources/CAD_Models/Cutting/Cutting_Support_Plate/Cutting_support_plate.FCStd
244.4 x 137.4 x 170.0 mm

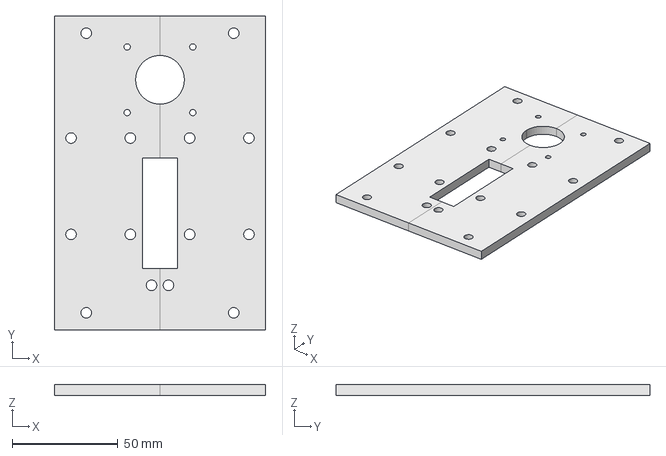
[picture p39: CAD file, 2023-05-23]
Sources/CAD_Models/Cutting/Moving_Plate/Moving_plate.FCStd
99.6 x 148.0 x 5.00 mm

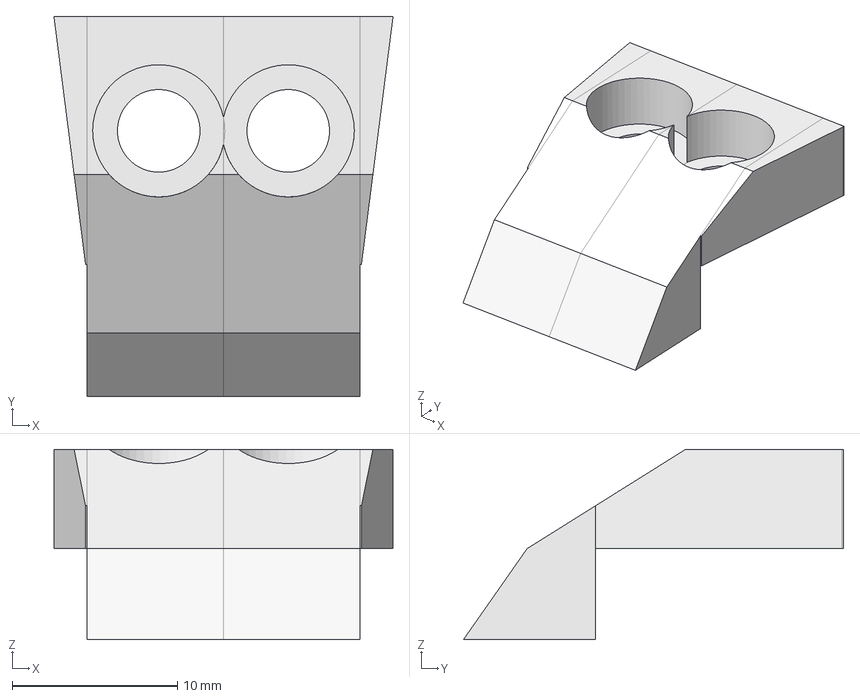
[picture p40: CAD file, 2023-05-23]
Sources/CAD_Models/Cutting/Slope/Slope.FCStd
20.5 x 23.0 x 11.5 mm

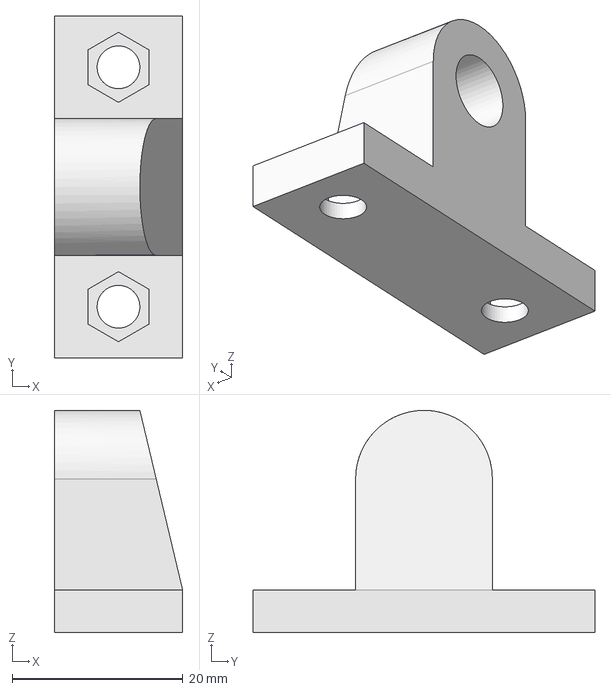
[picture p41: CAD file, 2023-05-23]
Sources/CAD_Models/Cutting/STUB_Support/Stub_support.FCStd
15.0 x 40.0 x 26.0 mm

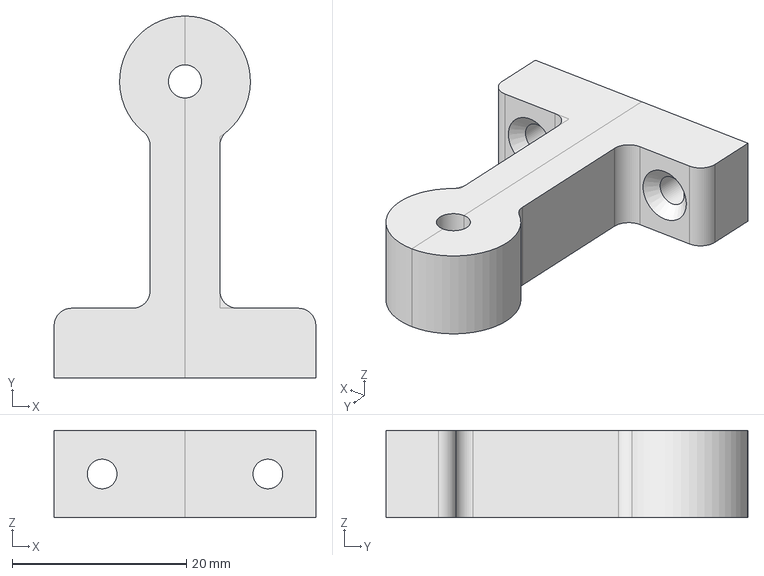
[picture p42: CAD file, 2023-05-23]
Sources/CAD_Models/Distribution/Guiding_Pipe/Straight_Tube_Support/Straight_Tube_Support.FCStd
30.0 x 41.5 x 10.0 mm

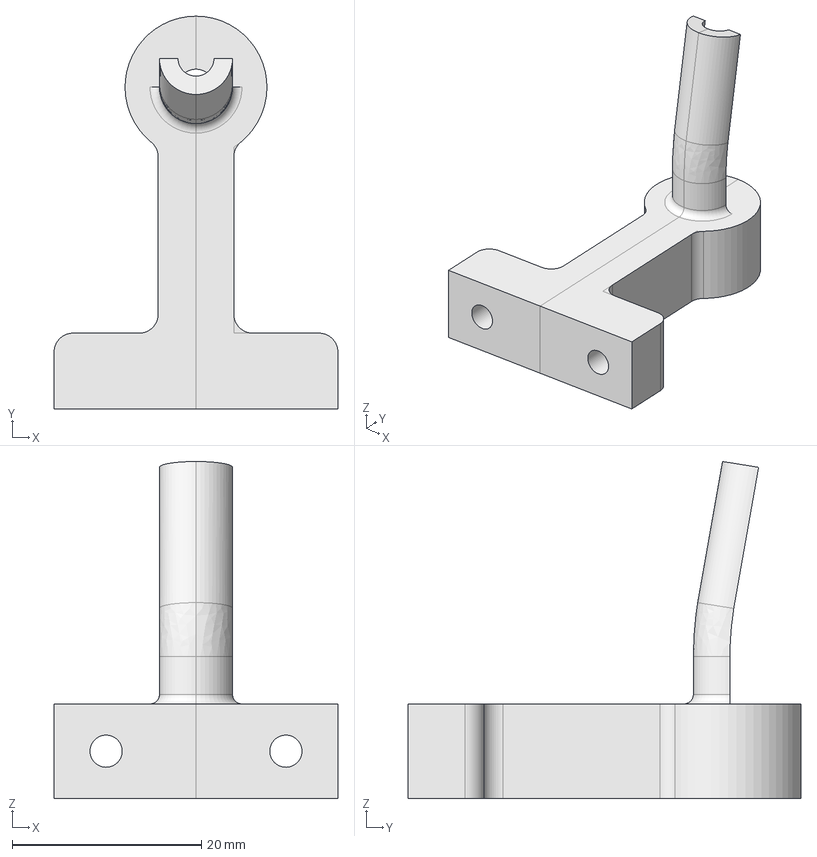
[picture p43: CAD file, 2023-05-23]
Sources/CAD_Models/Distribution/Guiding_Pipe/Tube_Support_With_Angle/Tube_Support_With_Angle.FCStd
30.0 x 41.5 x 35.6 mm

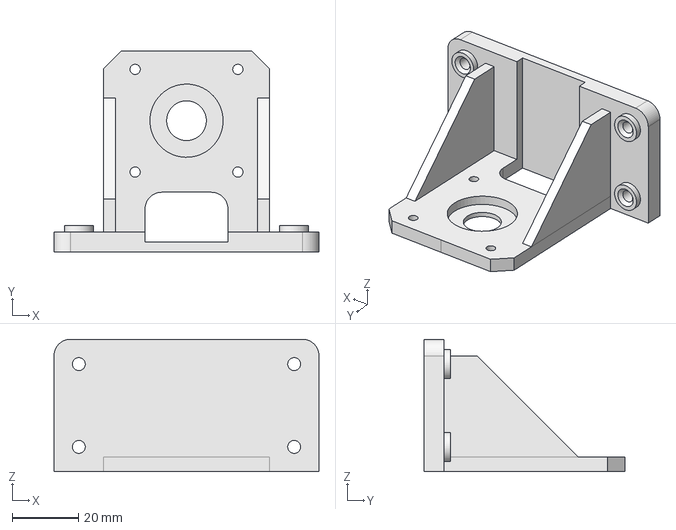
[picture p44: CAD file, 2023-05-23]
Sources/CAD_Models/Distribution/Motor_Support/Motor_Support.FCStd
80.0 x 60.6 x 40.0 mm

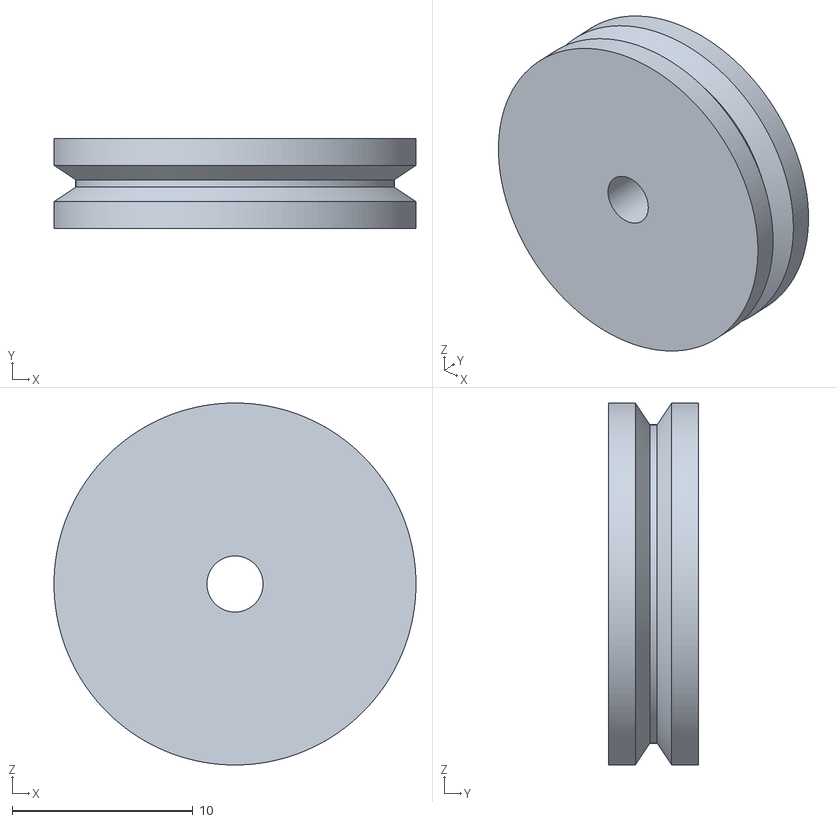
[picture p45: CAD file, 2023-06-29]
Sources/CAD_Models/Distribution/Wire_Tensionner/Rollers/Roller_Without_Bearing.stl
20.0 x 5.00 x 20.0

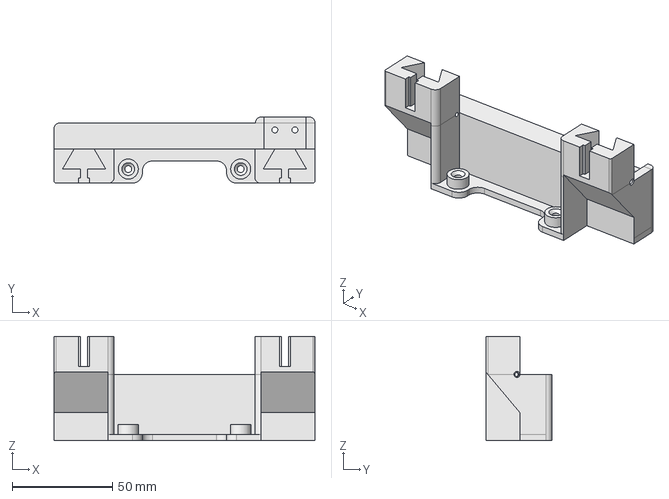
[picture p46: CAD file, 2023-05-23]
Sources/CAD_Models/Distribution/Wire_Tensionner/Wire_Tensionner_Bottom/Wire stainer bottom.FCStd
130.0 x 33.0 x 52.0 mm

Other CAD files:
Sources/CAD_Models/Distribution/Wire_Tensionner/Wire_Tensionner_Top/Wire stainer top.FCStd
Sources/CAD_Models/Power_Supply/Emergency_Button/Emergency_Button_Bottom/Emergency Button Bottom.FCStd
Sources/CAD_Models/Power_Supply/Emergency_Button/Emergency_Button_Top/Emergency_Button_Top.FCStd
Sources/CAD_Models/Power_Supply/Switch_Case/Switch_Case_bottom/Switch_Case_Bottom.FCStd
Sources/CAD_Models/Base_Plate/Base_Plate/Base_plate.dxf
Sources/CAD_Models/Base_Plate/Base_Plate/Base_plate.stl
Sources/CAD_Models/Base_Plate/Base_Plate_Legs/Base_plate_legs.dxf
Sources/CAD_Models/Base_Plate/Base_Plate_Legs/Base_plate_legs.stl
Sources/CAD_Models/Base_Plate/Breadboard_Corner_Anchor/Breadboard_Corner_Anchor.stl
Sources/CAD_Models/Cutting/Blade_Holder/Blade_holder.stl
Sources/CAD_Models/Cutting/Cam/came.stl
Sources/CAD_Models/Cutting/Cutting_Support_Plate/Cutting_support_plate.dxf
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

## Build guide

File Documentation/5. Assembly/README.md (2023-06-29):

# Assembly
The following lines will give you an overview of how is assemble the machine. 
Notice that a [Maintenance manual](././Sources/Documents) is available which will explain how to disassemble the machine.

## Base Plate
You can find [here](../../Sources/CAD_Models/Base_Plate) the CAD files of the parts associated to the _Base plate system_

**ajouter photo montage nomenclature + sigle indiquant la techno de fabrication**

## Reel Support
You can find [here](../../Sources/CAD_Models/Reel_Support) the CAD files of the parts associated to the _Base plate system_
## Distribution
You can find [here](../../Sources/CAD_Models/Distribution) the CAD files of the parts associated to the _Base plate system_
## Cutting and Stripping
You can find [here](../../Sources/CAD_Models/Cutting) the CAD files of the parts associated to the _Base plate system_
## User Interface
You can find [here](../../Sources/CAD_Models/User_interface) the CAD files of the parts associated to the _Base plate system_

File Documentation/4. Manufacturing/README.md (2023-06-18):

# Prototype parts
<details>
  <summary>Prototype pictures</summary>
  
## Cutting and stripping system
  
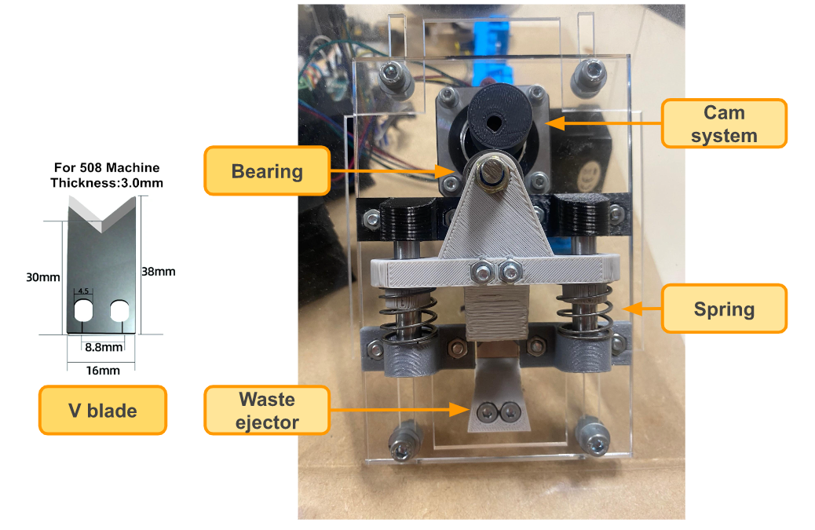
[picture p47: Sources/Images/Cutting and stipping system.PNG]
C&S system


## Bending
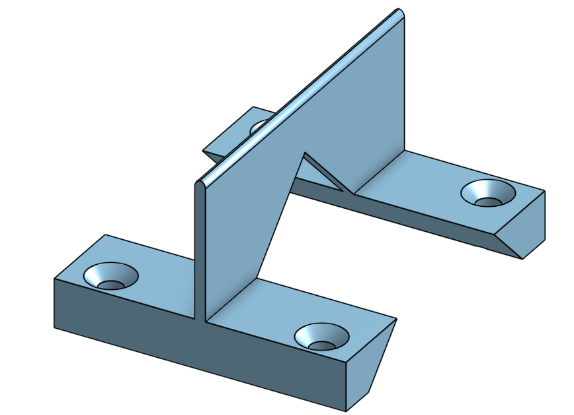
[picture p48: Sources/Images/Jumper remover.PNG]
Jumper remover

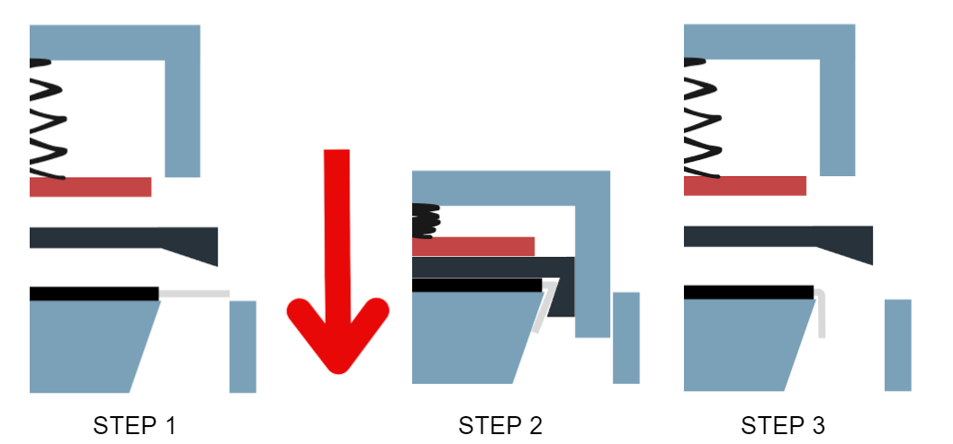
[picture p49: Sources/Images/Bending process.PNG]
Bending process

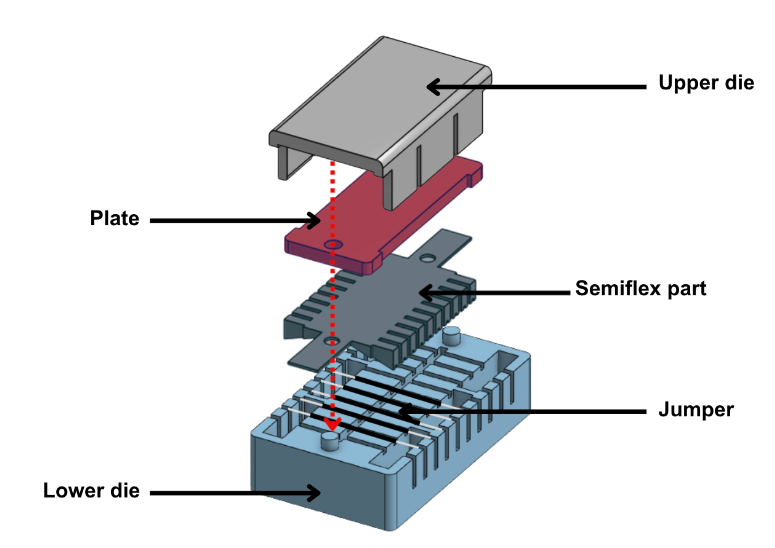
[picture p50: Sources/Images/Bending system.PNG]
Bending

  
## Final prototype :
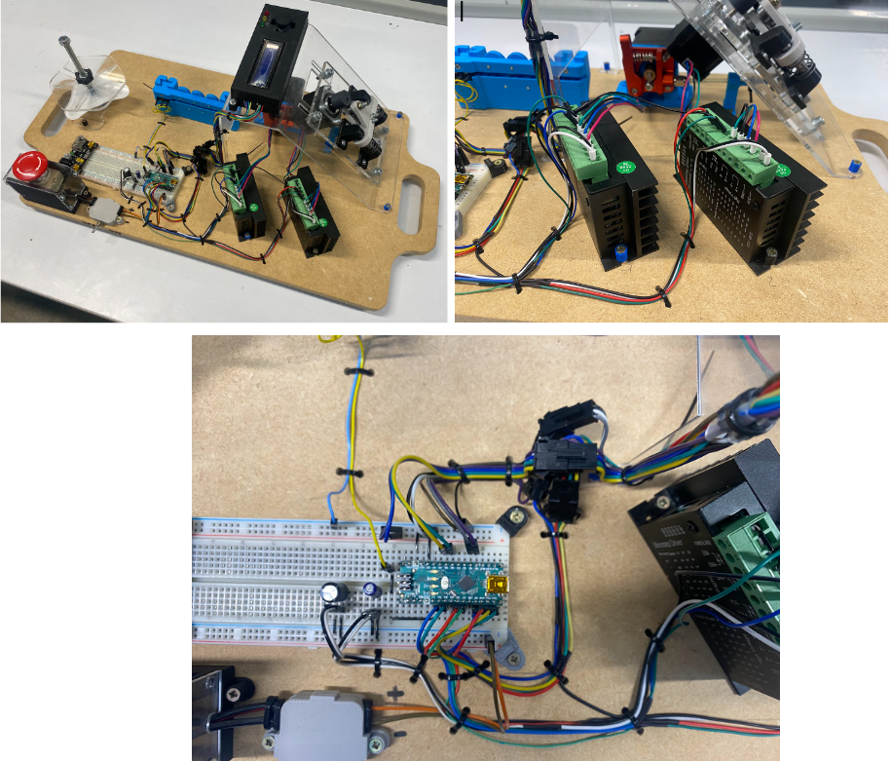
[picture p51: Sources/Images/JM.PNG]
Jumper machine


</details>

# **Processes for obtaining parts**

## **Distribution**
<details>
  <summary>3D-printing</summary>

  - Wire guides
  - Wire tensioners

</details>

## **Cutting**

<details>
  <summary>3D-printing</summary>
  
  - Maintenance of the slides
  - Sorting slope
  - Blade holder
  
</details>

<details>
  <summary>Laser cutting</summary>
  
  - Inclined tray
  - Sliding tray
  
</details>

## **Wiring**

<details>
  <summary>Welding</summary>
  
  - Wiring of the drivers
  
</details>

### *Bill of material (BOM)*
<details>
  <summary>Click to see the guideline</summary>

  You will find our _Bill Of Materials_ here : [BOM](../../Sources/Documents)

</details>

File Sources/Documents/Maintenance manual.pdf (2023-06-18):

# Maintenance manual PDP 12 - Jumper Machine

Clara HEID | Virgile MARTY | Florian BOULAY
Bastien VINCENT | Benoît VÉRAN

In this document, there will be compill all of our problems encountered by our group during the project. This manual will also provide a protocol to disassemble some parts and our potential guidelines for futur developpement of the project.

# GitHub Link (Click Here) (https://github.com/BenoitGI/Jumper-Machine-)

OnShape Link (Click Here) (https://cad.onshape.com/documents/e23f2a9b7d5cbfc350862d24/w/3bd71b5e537bce5bc2623e5e/e/d0d5c7eefa7db94f148151a4)

Maintenance Manual - Jumper Machine 2022/2023 | 1

# Malfunction

### The machine does not switch on?

Check if :
- the emergency button is unlock (rotate the button in the direction of the arrows)
- the switch is ON
- the breadboard’s power system is ON (a green light should light on)
- both of external power supply are connected to the power
- Verify the pins of the breadboard’s power alimentation, they should be like this :

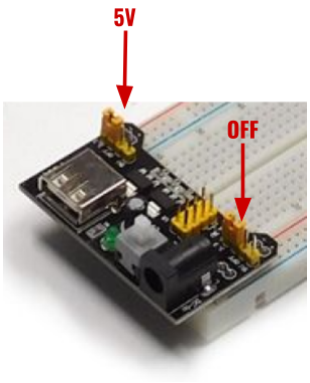
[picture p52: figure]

- Verify the connections between the switch and the 12V tracks of the breadboard The problem is fixed if the UI, green lights from each driver, leds on Nano and the green light of the breadboard’s alimentation are lit.
If the issue persists, use a multimeter to test the continuity on each wire.
If the issue persists, there is a defective component you need to identify.
Maintenance Manual - Jumper Machine 2022/2023 | 2

### Does the UI switch off, display the wrong information or not respond?

-Verify the connections between components according to the Electrical Diagram (in User Manual).
-Look at the pluggable wires, there may be a connection failure.
-Check if the plug systems are correctly connected (the color should make sense between the two sides).

### The thread does not come straight out of the machine

The tightened distribution system is perhaps a little loose. follow the steps :
- Loosen the 2 screws.
- press the tensioner top on the wire (not too much).
- keeping pressure on tensioner top while you tight the two screws

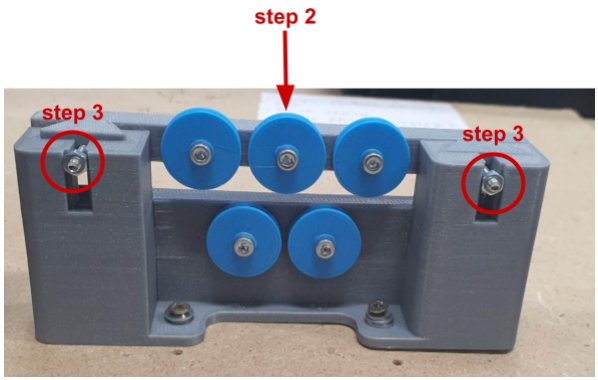
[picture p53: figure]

Maintenance Manual - Jumper Machine 2022/2023 | 3

### The wire dips between the hose and the blades

In some bad case scenarios, the wire could dive under the blade at the exit of the blade. This issue is often the result of a bad adjustment of the height above the guiding pipe. To fix the problem, we advise to set the height offset of the moving plate.
To do this (easier if there are two of you) :
- loosen the 4 screws
- adjust the height of the moving plate, the wires should pass 1 mm above the bottom blade
- while keeping the moving plate, tighten the 4 screws (start by the diagonal)
- test if the machine works again with 1 jumper of length 3.

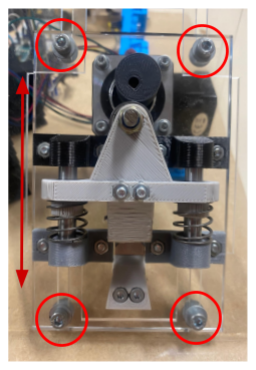
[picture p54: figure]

Note that we add under our tube support with angle some round plate washers to give us more flexibility in the setting of the moving plate.

You need to loose the 4 screws of the “moving plate”. Then, set the height manually, the wire should pass 1 mm above the bottom blade.

Maintenance Manual - Jumper Machine 2022/2023 | 4

### How do you fit the wire into the system?

Currently, the system has been designed for wire type AWG 23, we aren't sure the machine will work well if another wire is used.
To set up the system, follows the steps in the right order :
- Install the wire reel on the reel rack
- remove the tensioner top of the distribution system.
- pass the wire through the distribution system.
- put back tensioner top and keep pressure on it while you tight the two screws
- with one hand, press the extrudeur to loose the grip of the counter driving wheel. With your other hand, push the wire inside the first hole until the end of the wire has passed the driving wheel and has entered the second hole.

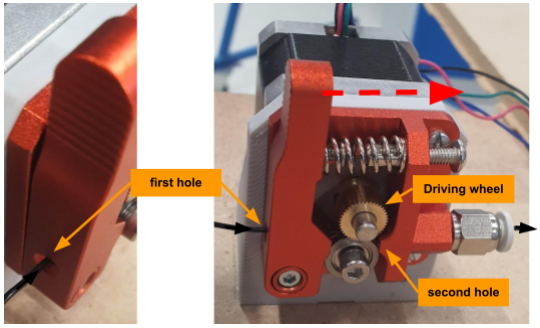
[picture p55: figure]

- activate the “push wire” function with the UI.

### The machine doesn’t strip the wire

It’s certainly caused by a malfunction of the stripping offset or an incorrect adjustment of the “set denude” sub-menu. (Available on GitHub → Documentation→ Design → Structural Model → Software → UI)

When you enter the “set denude” menu, you will be able to set the blade to the position of stripping, where it is just cutting the sheath.
The first step will be to ensure a small part of the wire is stepping out of the machine (it will be cut of when you run the program, so you don’t need to much wire because it’s waste).
Maintenance Manual - Jumper Machine 2022/2023 | 5

Then once you enter the menu, you can move the cam with the joystick in one way, the way it will cut during the program (you can turn back of course but it will be blocked at its original position to avoid to turn in way to strip and another way to cut during the program). The more you push the joystick on its side, the more the cam turns, to get close faster but position it more precisely. The screen is showing the number of steps the wire moved from the origin.

Once you get the blades closer to the wire, move them until they can’t move anymore unless the cut the core of the wire. If you found the stripping position, you can press the joystick. You will leave the menu; the cam will turn back to its origin and the screen will show the position of stripping (in number of steps).

It’s recommended to run the program with only one jumper at the time of the desired length to check it’s working, and repeat it once or twice. If it’s not working, change the position of stripping (bigger from the previous position if not cutting enough the sheath, smaller than the previous position if cutting too much and biting into the core).

### The movement of the wire is blocked by the blades

When something blocks the wire, the driving wheel of the extruder will slippage resulting in no movement of the wire. In the great majority of cases, it’s due to the V Blades which attack the core of the wire during the stripping phase.
When you observe this phenomena, stop the process and redo the set denude process.
Maintenance Manual - Jumper Machine 2022/2023 | 6

# Disassemble

If you need access under the cutting support plate.
Follow the step in the right sequence:
- Be assured that the jumper Machine is power off (no led lit on the Arduino card and drivers)
- Disconnect the 4 plugs at the bottom of the cutting support plate, it will disconnect the UI.

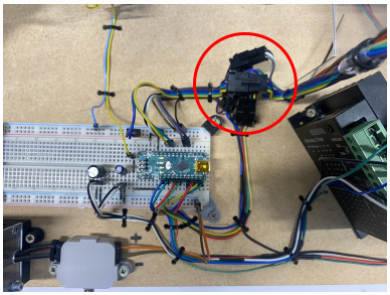
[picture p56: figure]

- Disconnect the wires of the motor by unplug the green plastic plug of the driver
- You can now loosen the 4 screws which maintain the cutting support plate fix with the base plate.
- For reassembling, make the steps in the reverse order. Don’t forget the spacer for the 4 screws.
Maintenance Manual - Jumper Machine 2022/2023 | 7

### Replace worn blades with new ones

After some time, the blades may have worn down. To change them, Follow the step in the right sequence:
- Be assured that the jumper Machine is power off (no led lit on the Arduino ship and drivers)
- Disconnect the wires of the motor by unplug the green plastic plug of the driver
- Loosen the 4 screws from the moving plate.
- Loosen the 2 screws of the bottom V Blade and take it off.
- Then, loosen the 2 screws of the upper V Blade. Be cautious during this step, there is a spring under tension behind the blade. Take off the upper blade

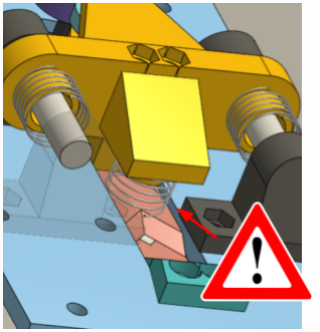
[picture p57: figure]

- For reassembling, make the steps in the reverse order. The V Blades need a height adjustment during the reassemble. Our only solution to have a good adjustment for the moment is to do it by trial and error. Test with the process of one jumper length 3.
Maintenance Manual - Jumper Machine 2022/2023 | 8

# Line of research

The following is a non-exhaustive list of areas for improvement to make the machine more reliable and resilient in our opinion. Feel free to take it in consideration or not.

### Refine the stripping system

The current stage of our stripping system was convenient for us because he uses the same motor to cut and strip the wire. However, the two functions could be separate physically with two motors instead of one. Moreover, the “set denude” system isn’t reliable:

- Firstly, it isn’t the same from one start to another with the reboot of the machine. We know that we use only wire AWG23 so there should be a way to always strip the wire to the same depth, regardless of the number of restarts.
- Secondly, we have an issue with the motor step with a slight offset created by each stripping (hence the addition of a micro-step in the code to try to cancel it out). See if the problem isn't due to driver step resolution. Read the final deliverable (on the GitHub) to know more about this issue.

### Automate the bending system

Our first objective was to create a completely automatic system, due to our planning this wasn’t possible, and we focus on the cutting and stripping system. To automate the system, we need to Automate bending: we do a lot of knowledge to find a system which work manually, see if this can be transposed to automation

### incorporated a sorting system at the machine output

Currently, everything exits the machine through the blades, whether it's sheaths or jumpers. It’s not convenient and it can be a risk for the process (one jumper block between the blade for instance). We add a slop to the bottom V Blade for minimize the problem for a time. However, it’s not a definitive solution at this issue. A reliable sorting system could be set up to separate sheath and jumper and secure the end of the process.

### Creation of a machine housing around the blades and electronics

This machine is composed of blades, motors and electronic which can explode (we already blow up a capacitor for instance). If we want the machine to be implement in an environment with people, it shall not be a risk both for people and the machine. You need to find out about the standards for this type of machine and create protections/housing accordingly.

Maintenance Manual - Jumper Machine 2022/2023 | 9

### Improve the tensioner system

We don't find the system of tensioner convenient when you need to feed the system with wire at the start. Moreover, the tension applied on the wire by the rollers isn’t the same at each set up. A standard force applied by a spring system should be way more resilient. And a system which opens like a chest, you pass the wire, then close it with a lock should be more convenient than the current system of disassembly.

### Fixer le support

The current cutting support plate is attached with the moving plate by 4 screws. We did this to allow us to adjust the height of the blade accordingly for our future modification. But it’s not a definitive system. The two plates should be merged when the functionalities of the machine will be done, and the best height knows. It will avoid another parameter to set up.

Maintenance Manual - Jumper Machine 2022/2023 | 10

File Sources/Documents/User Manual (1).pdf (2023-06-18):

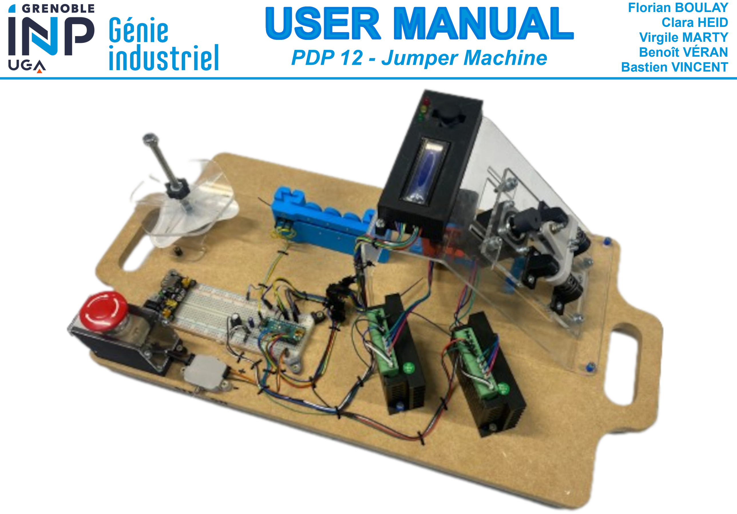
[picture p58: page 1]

### Florian BOULAY Clara HEID Virgile MARTY

Benoît VÉRAN PDP 12 - Jumper Machine | Bastien VINCENT

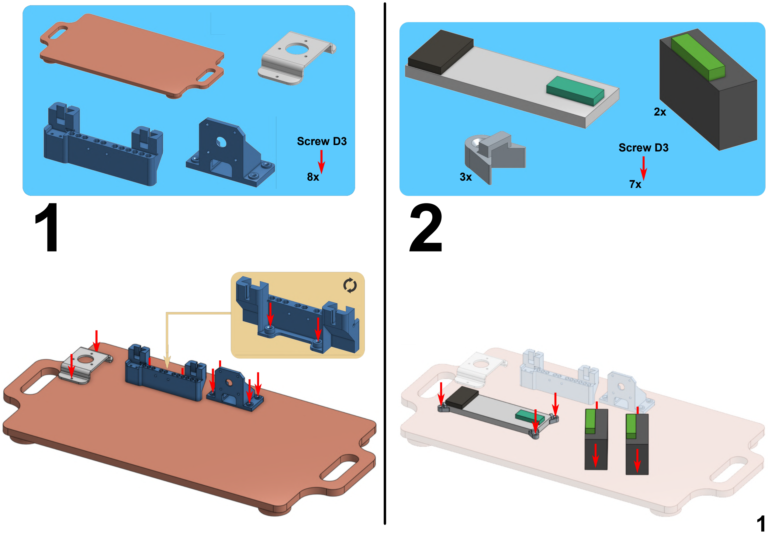
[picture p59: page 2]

Screw D3

8x

Screw D3

7x

2x

3x
1 | 2

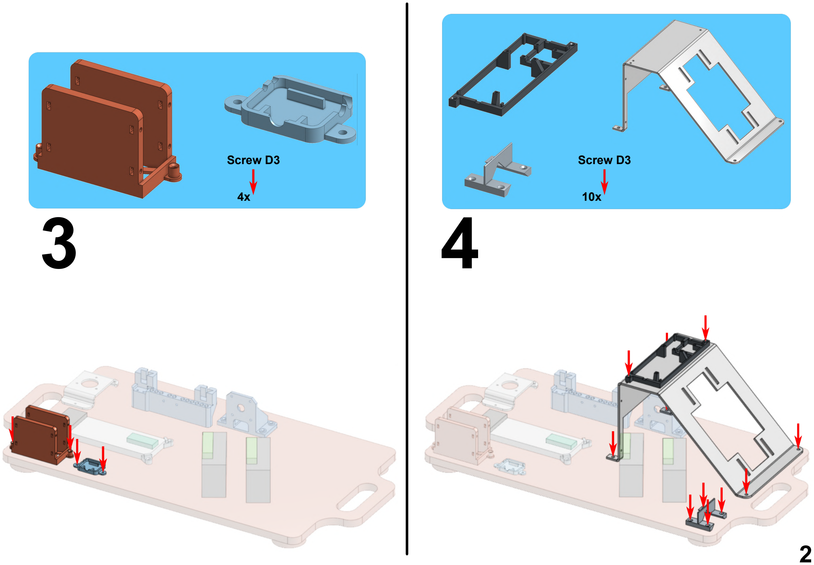
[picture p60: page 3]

Screw D3

4x

Screw D3

10x
3 | 4

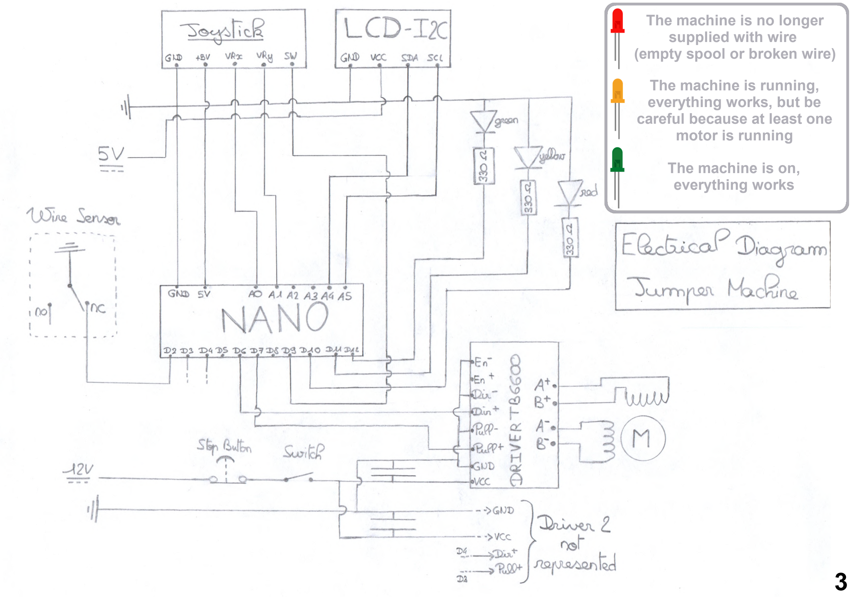
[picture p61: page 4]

The machine is on,

### everything works

The machine is running,

### everything works, but be careful because at least one motor is running

### The machine is no longer supplied with wire (empty spool or broken wire)

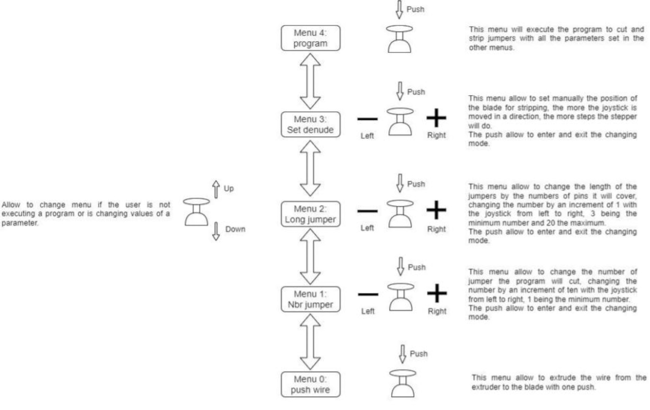
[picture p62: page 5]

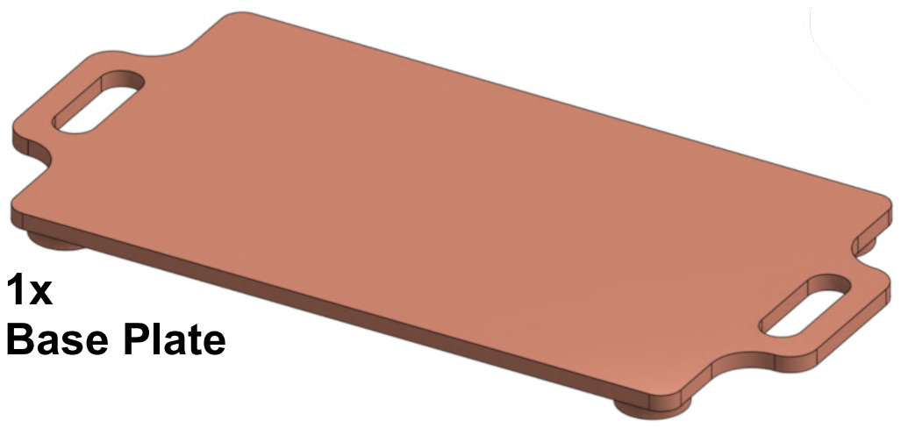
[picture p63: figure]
1x Base Plate
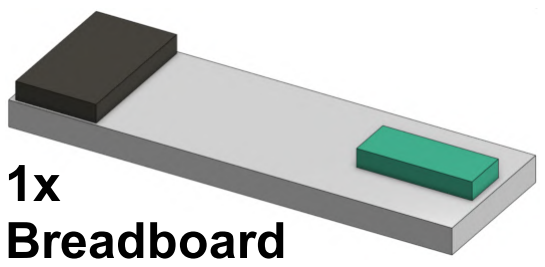
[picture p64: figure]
1x Breadboard
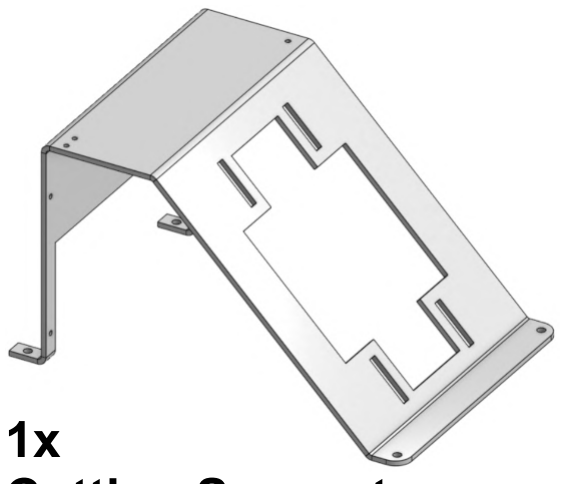
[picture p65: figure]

Cutting Support

2x
Driver

1x
Emergency Stop Button

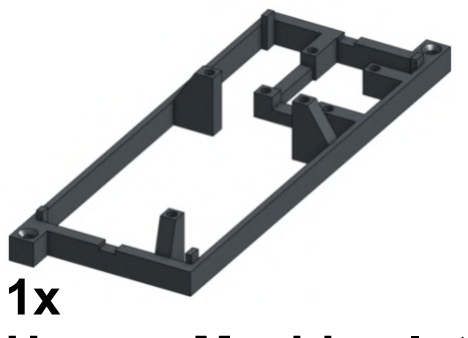
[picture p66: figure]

Human-Machine Interface

1x
Jumper Remover

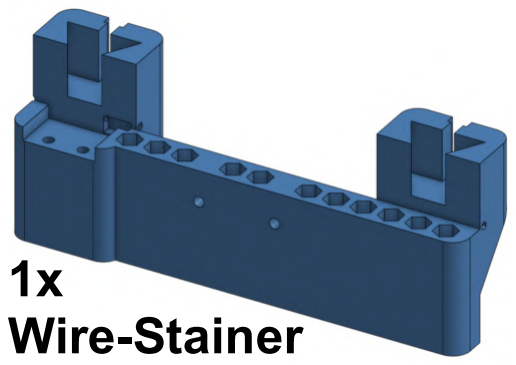
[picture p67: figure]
1x Wire-Stainer

1x
Motor Support

1x
Reel Support

1x
Switch

3x
Tie

29x
Screw D3

# More Instructions

# 1) connect the power cable to the arduino board 2) connect the 5A power supply to the emergency stop button 3) check that the emergency stop button is up 4) turn on the arduino board 5) turn on the switch

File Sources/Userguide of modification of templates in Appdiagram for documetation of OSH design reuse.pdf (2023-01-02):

The process of registration of edited templates in Appdiagrams

1- Use the guideline and templates for documentation from OPEN-NEXT GitHub for your project and rename it in your GitHub account

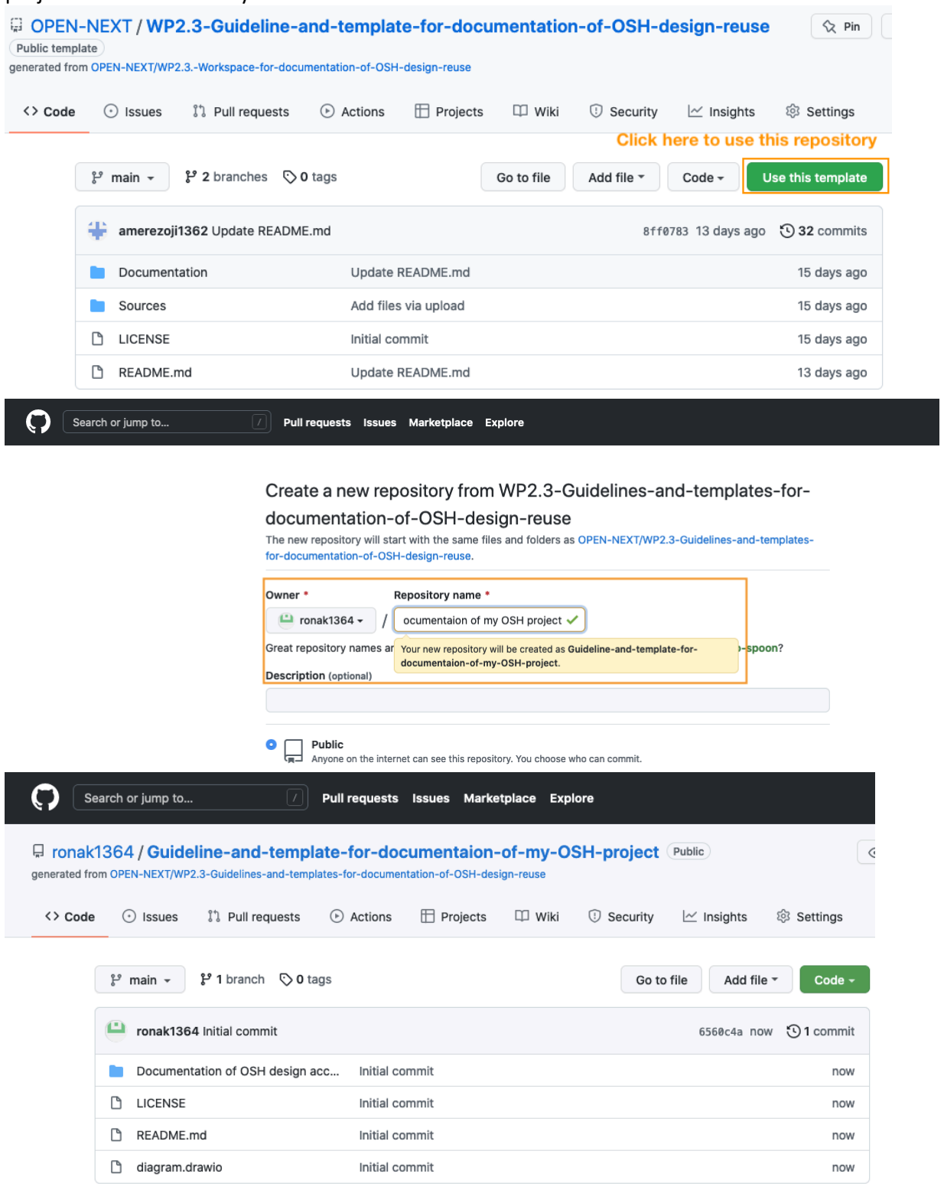
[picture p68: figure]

2- Then, you start to create your documentation, and you can modify the templates on App diagram by clicking on “Edit As New”

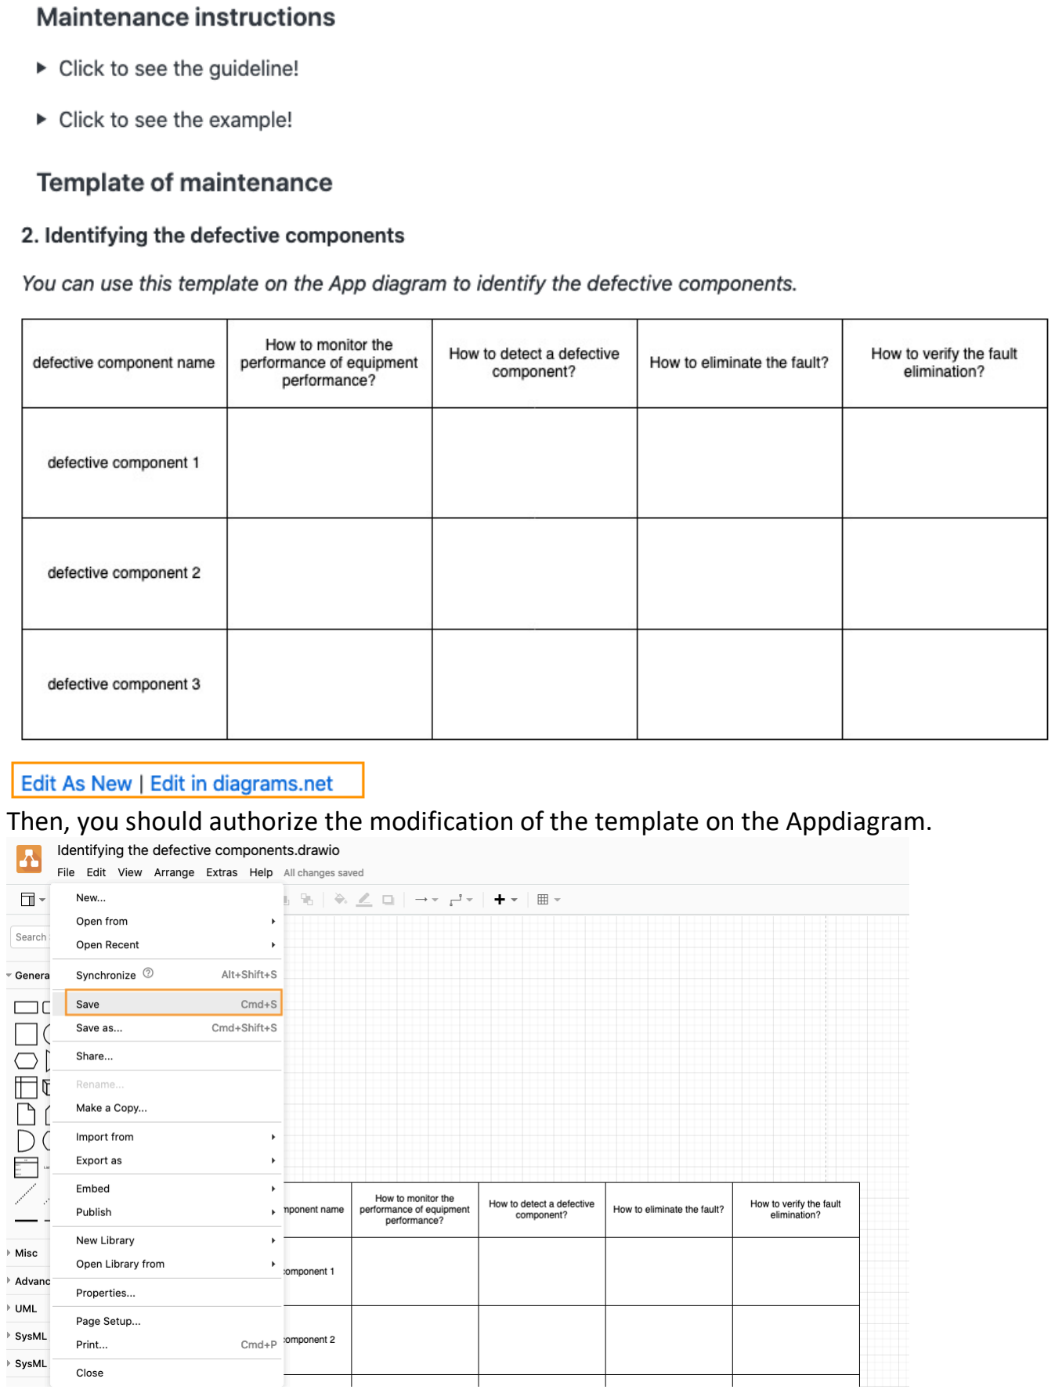
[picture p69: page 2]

Then, you should authorize the modification of the template on the Appdiagram.

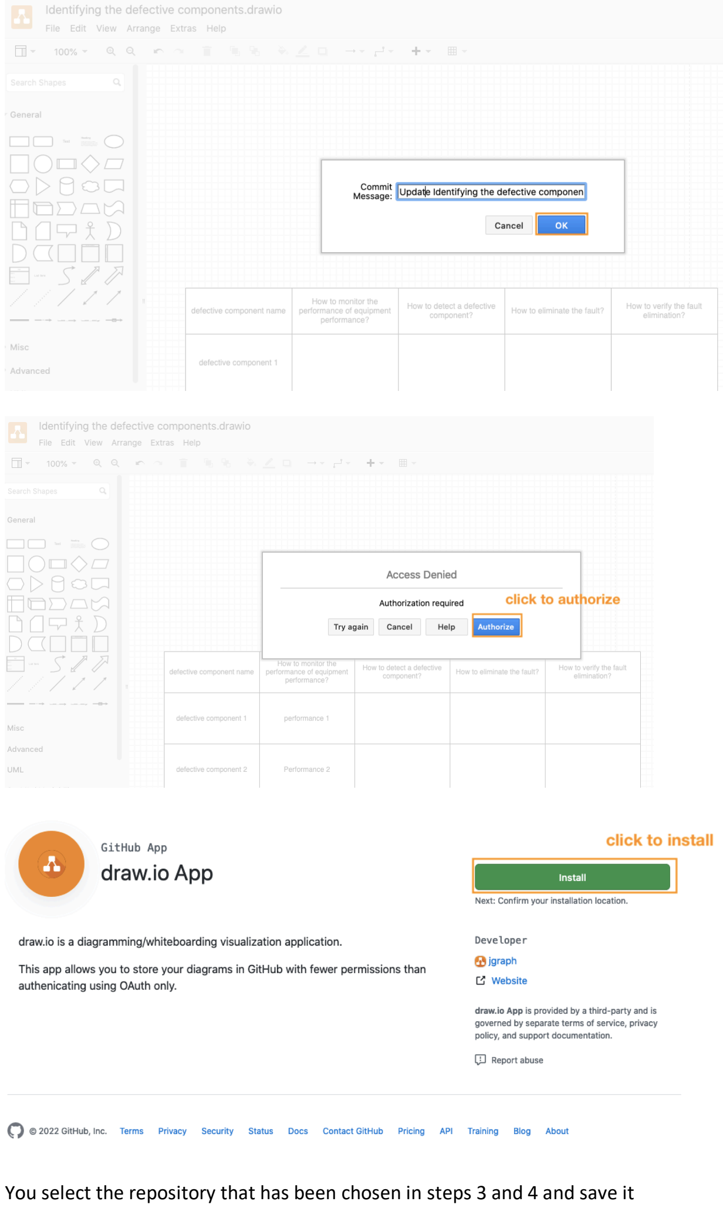
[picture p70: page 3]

You select the repository that has been chosen in steps 3 and 4 and save it

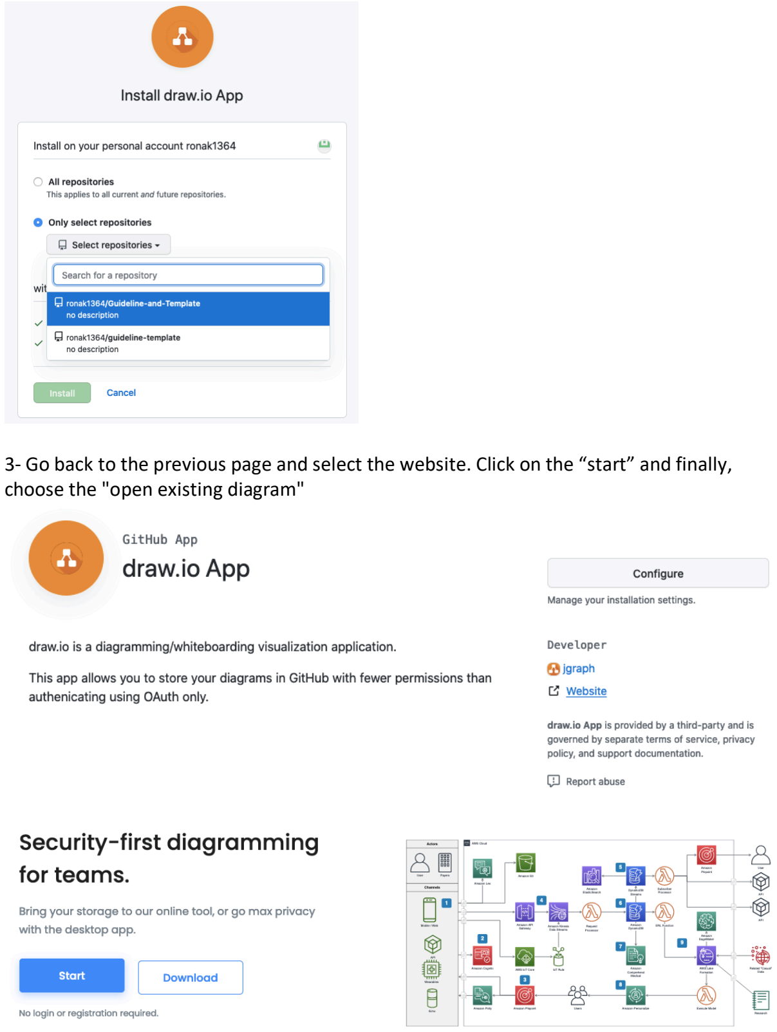
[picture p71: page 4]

3- Go back to the previous page and select the website. Click on the “start” and finally, choose the "open existing diagram"

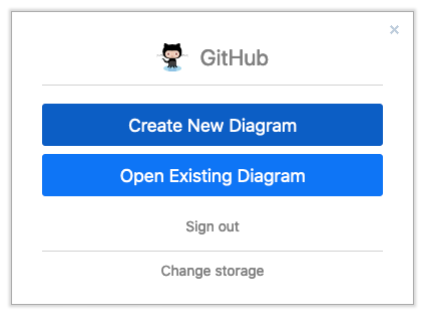
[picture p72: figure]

4- In this step, you should select the repository of step 4 that entitled “Guideline and Template”

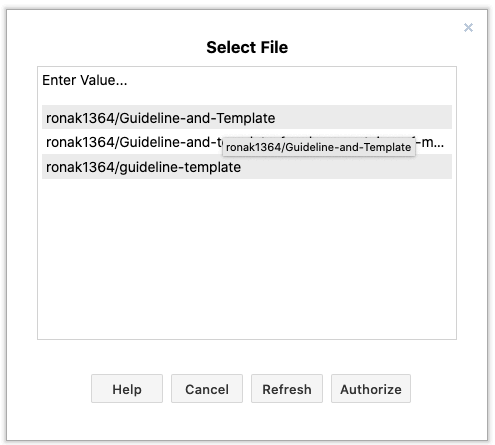
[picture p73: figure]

You should authorize it according to the selected Appdiagram that you wanted to modify in
step 6.
For example, I wanted to modify the Appdiagram that entitled “identifying the defective components”.

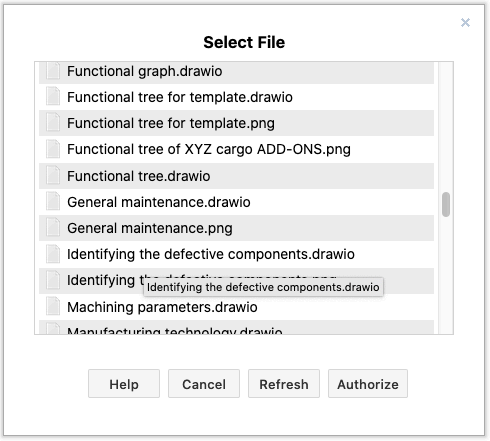
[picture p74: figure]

5- So, you can modify the template completely on Appdiagram and save it.

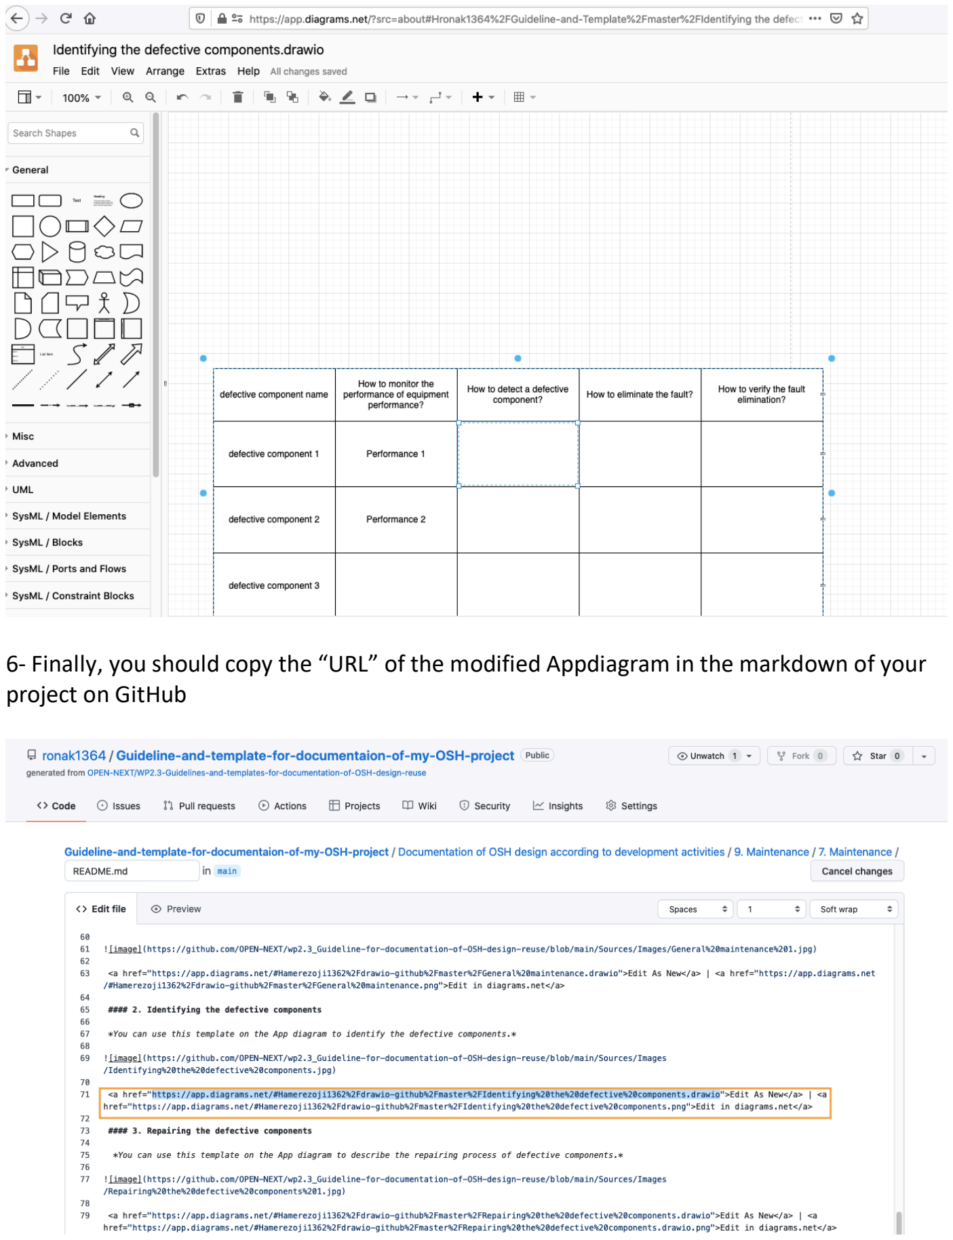
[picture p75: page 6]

6- Finally, you should copy the “URL” of the modified Appdiagram in the markdown of your project on GitHub

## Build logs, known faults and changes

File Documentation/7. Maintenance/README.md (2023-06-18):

# **Maintenance**

You will find here a maintenance manual : [Maintenance manual](../../Sources/Documents)

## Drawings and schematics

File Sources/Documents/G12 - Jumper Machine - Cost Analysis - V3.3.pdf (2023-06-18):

# G12 - Jumper Machine - Cost analysis - V3.3

# Bill of materials (B.O.M.)

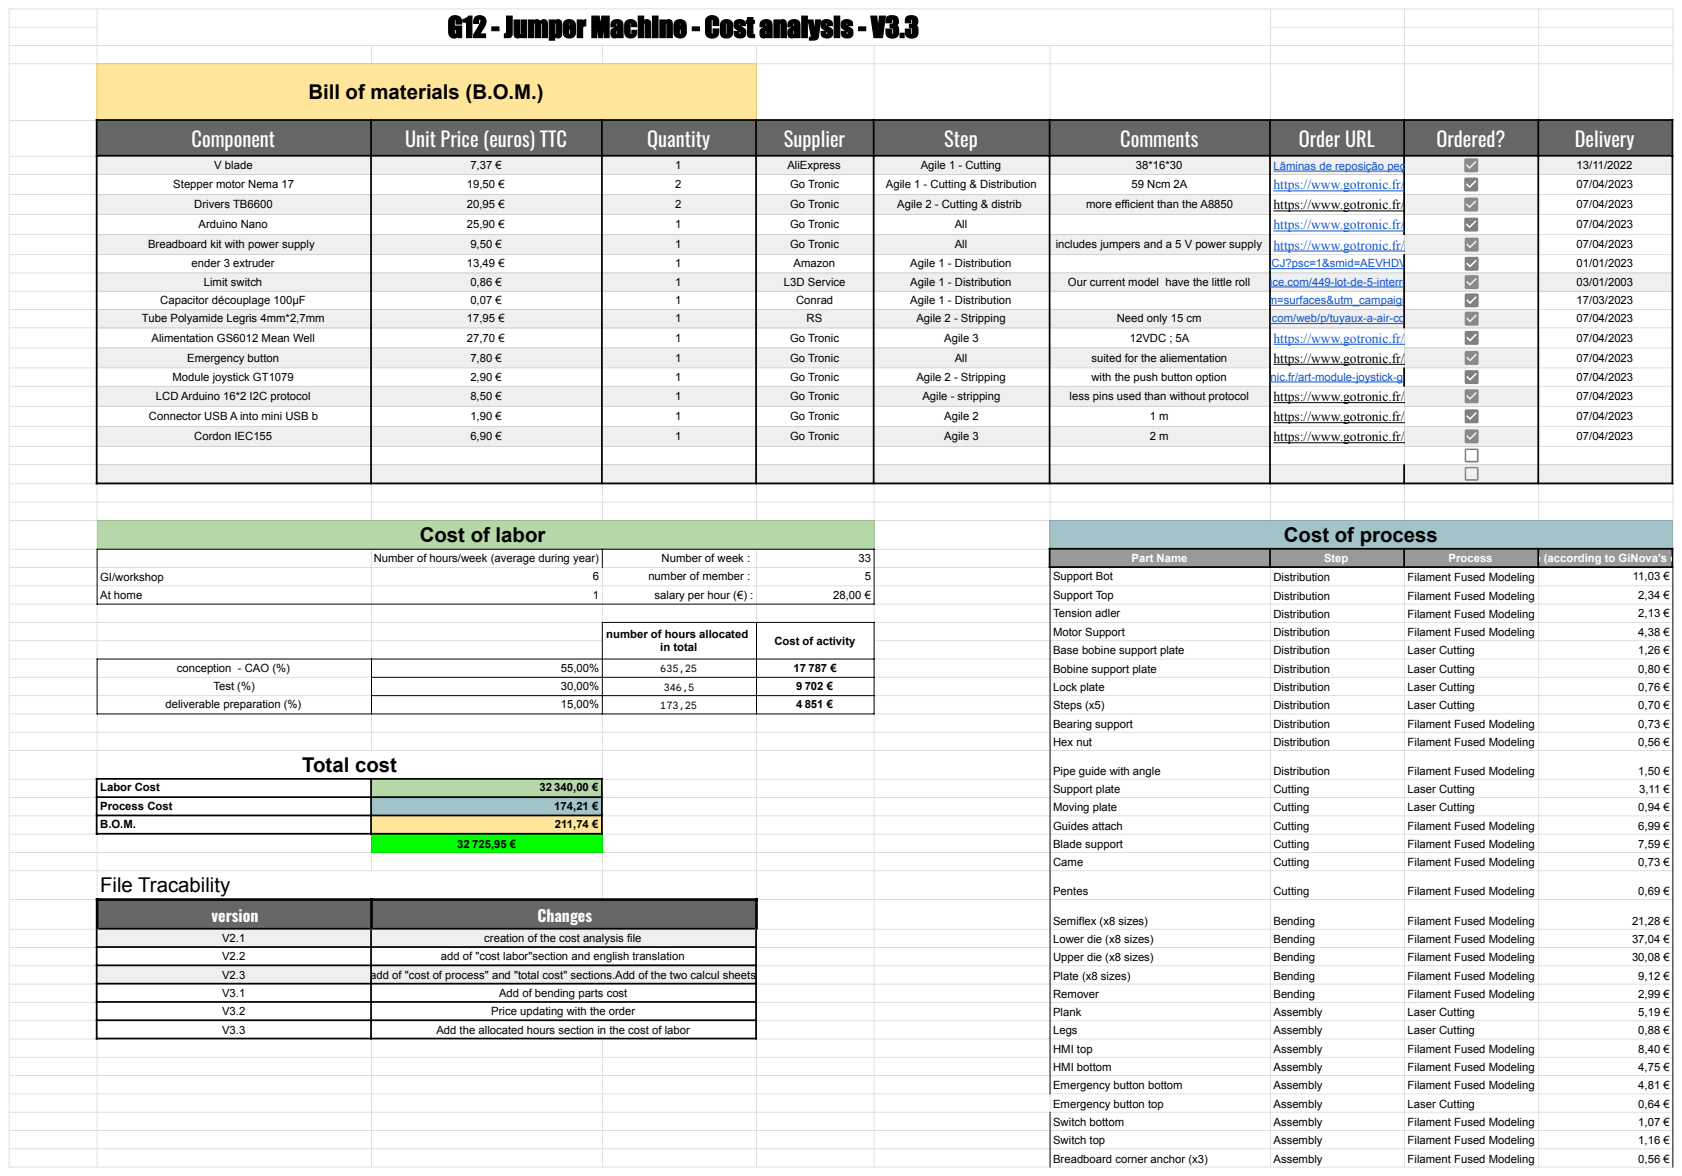
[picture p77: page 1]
Component; Unit Price (euros) TTC; Quantity; Supplier; Step; Comments; Order URL; Ordered?; Delivery; V blade; AliExpress; Agile 1 - Cutting; Lâminas de reposição peças lâmina de faca de aço para swt508c swt508e fio descascando peeling máquina de corte| | - AliExpress 13/11/2022; Stepper motor Nema 17; Go Tronic; Agile 1 - Cutting & Distribution; 59 Ncm 2A; https://www.gotronic.fr/art-moteur-17hs19-2004s-18355.htm 07/04/2023; Drivers TB6600; Agile 2 - Cutting & distrib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

number of hours allocated

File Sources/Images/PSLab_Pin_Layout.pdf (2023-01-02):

# Pocket Science Lab V5

# Pin Layout Diagram

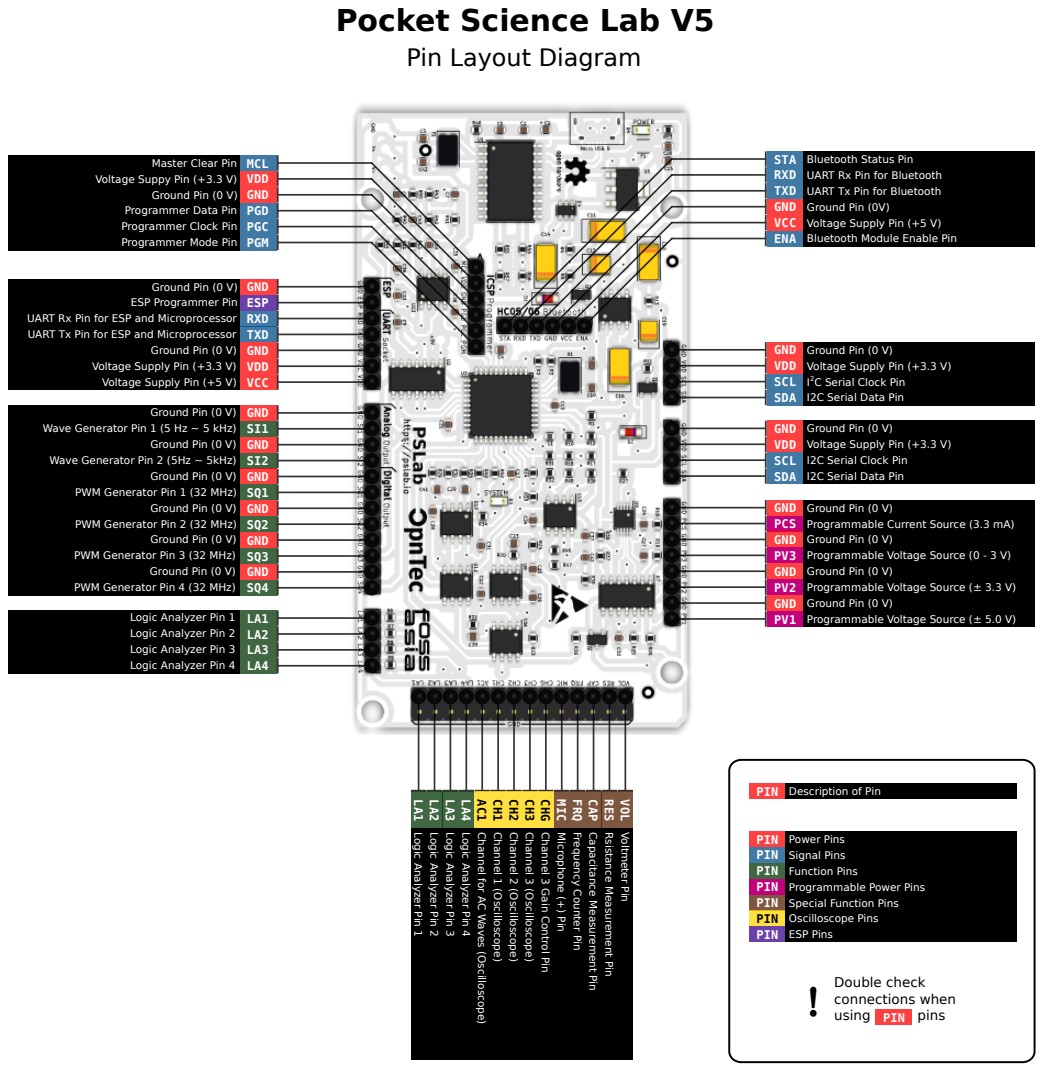
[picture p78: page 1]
2 SCL; C Serial Clock Pin; Channel 1 (Oscilloscope) CH1; Channel 2 (Oscilloscope) CH2; Channel 3 (Oscilloscope) CH3; Master Clear Pin MCL; STA Bluetooth Status Pin; PIN; using; pins

Voltage Suppy Pin (+3.3 V) VDD

RXD UART Rx Pin for Bluetooth
TXD UART Tx Pin for Bluetooth
GND Ground Pin (0V)
VCC Voltage Supply Pin (+5 V)
ENA Bluetooth Module Enable Pin

Ground Pin (0 V) GND
Programmer Data Pin PGD
Programmer Clock Pin PGC
Programmer Mode Pin PGM

ESP Programmer Pin ESP

UART Rx Pin for ESP and Microprocessor RXD
UART Tx Pin for ESP and Microprocessor TXD

GND Ground Pin (0 V)
VDD Voltage Supply Pin (+3.3 V)
SDA I2C Serial Data Pin

Voltage Supply Pin (+3.3 V) VDD
Voltage Supply Pin (+5 V) VCC

Wave Generator Pin 1 (5 Hz ~ 5 kHz) SI1

SCL I2C Serial Clock Pin

Wave Generator Pin 2 (5Hz ~ 5kHz) SI2

PWM Generator Pin 1 (32 MHz) SQ1

PCS Programmable Current Source (3.3 mA)
PV3 Programmable Voltage Source (0 - 3 V)
PV2 Programmable Voltage Source (± 3.3 V)
PV1 Programmable Voltage Source (± 5.0 V)

PWM Generator Pin 2 (32 MHz) SQ2

PWM Generator Pin 3 (32 MHz) SQ3

PWM Generator Pin 4 (32 MHz) SQ4

Logic Analyzer Pin 1 LA1
Logic Analyzer Pin 2 LA2
Logic Analyzer Pin 3 LA3
Logic Analyzer Pin 4 LA4

PIN Description of Pin

Channel for AC Waves (Oscilloscope) AC1

Channel 3 Gain Control Pin CHG

Microphone (+) Pin MIC

Frequency Counter Pin FRQ

Capacitance Measurement Pin CAP

Rsistance Measurement Pin RES

Voltmeter Pin VOL

PIN Power Pins
PIN Signal Pins
PIN Function Pins
PIN Programmable Power Pins
PIN Special Function Pins
PIN Oscilloscope Pins
PIN ESP Pins
Double check
connections when

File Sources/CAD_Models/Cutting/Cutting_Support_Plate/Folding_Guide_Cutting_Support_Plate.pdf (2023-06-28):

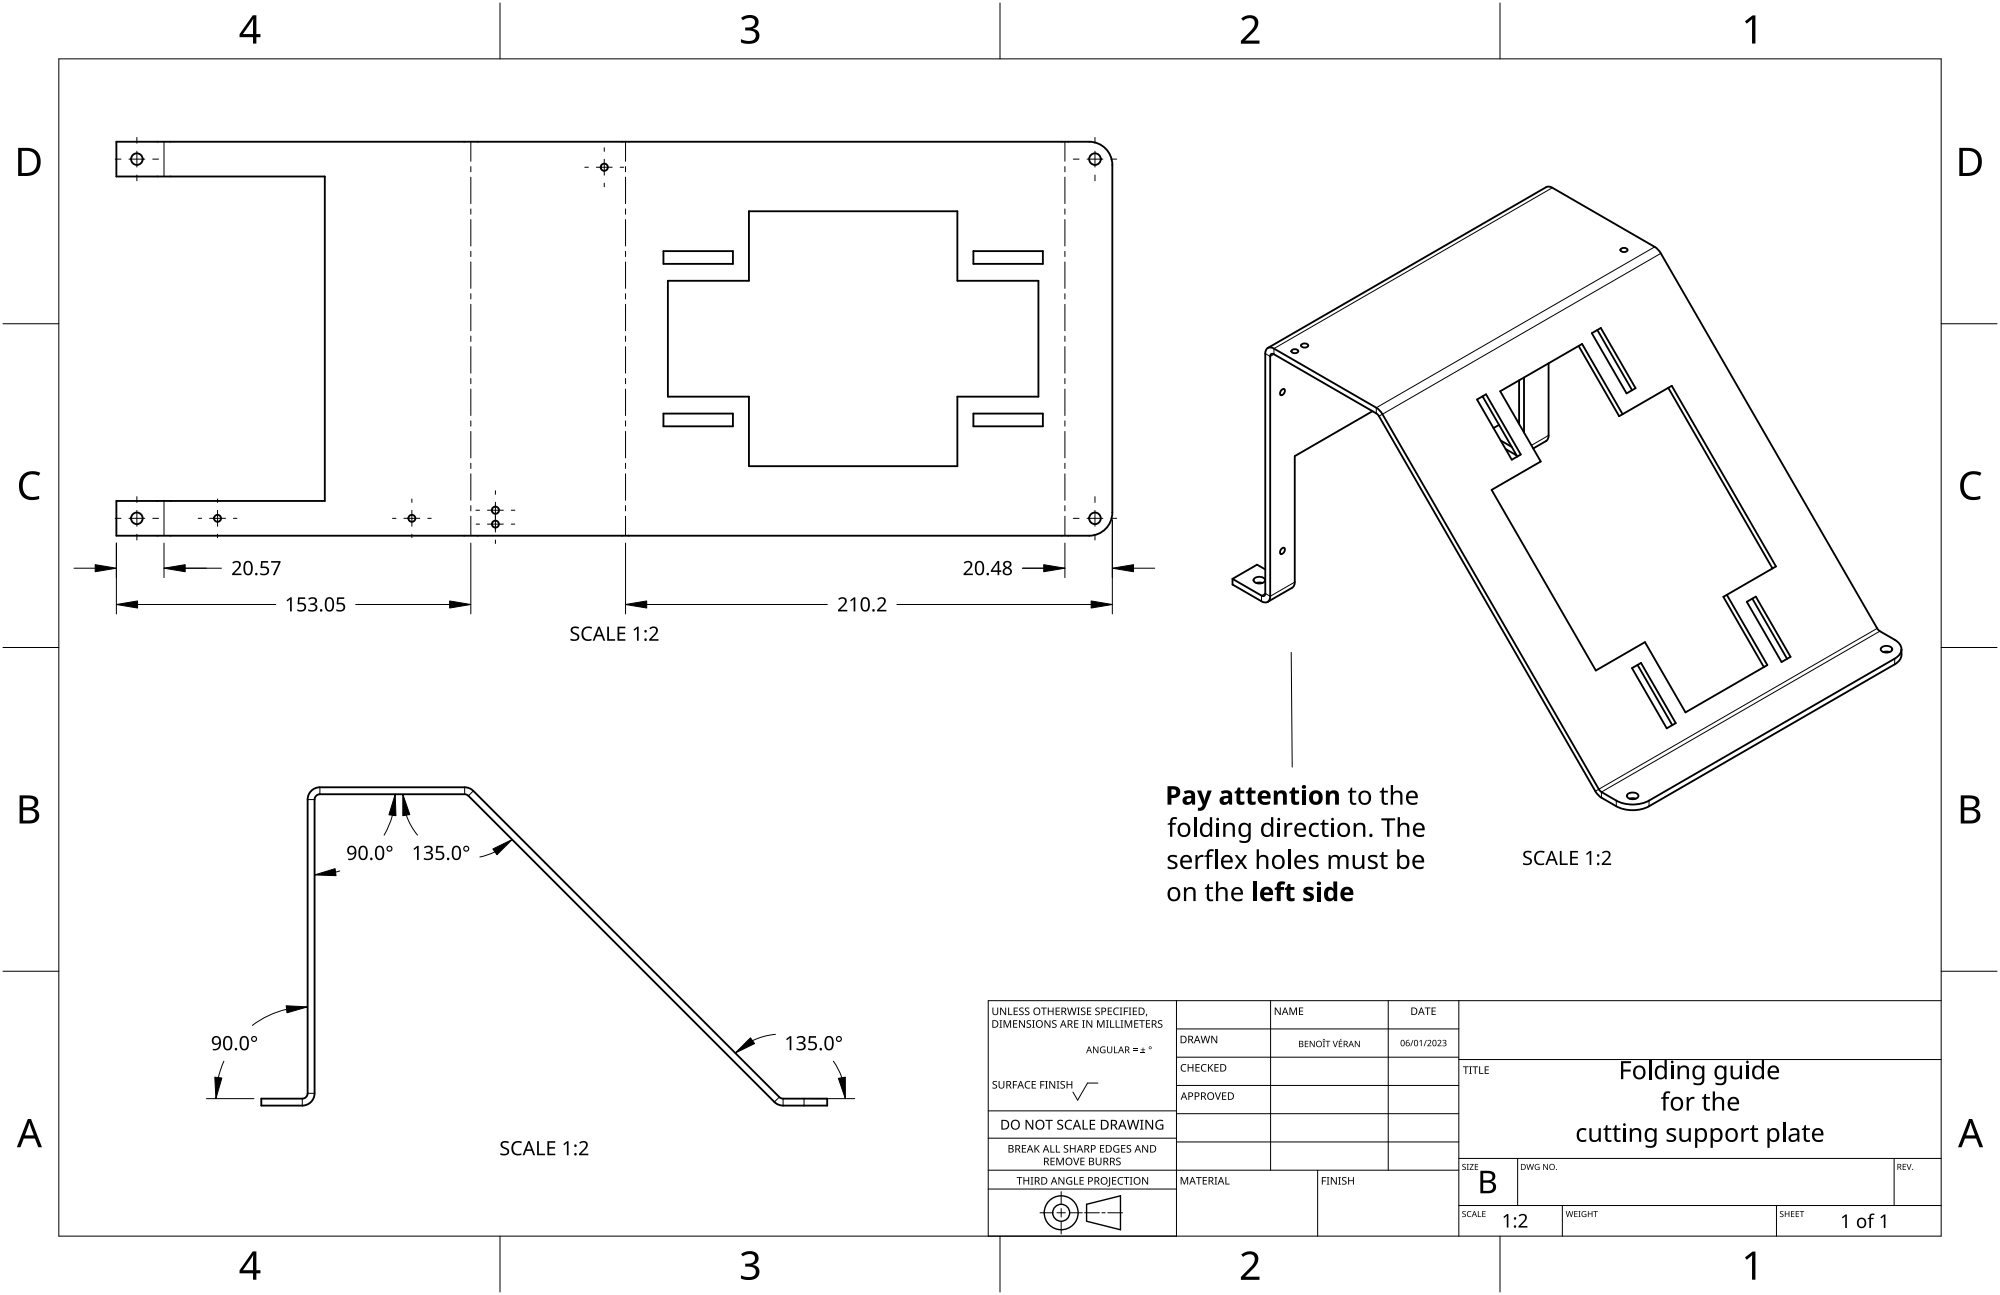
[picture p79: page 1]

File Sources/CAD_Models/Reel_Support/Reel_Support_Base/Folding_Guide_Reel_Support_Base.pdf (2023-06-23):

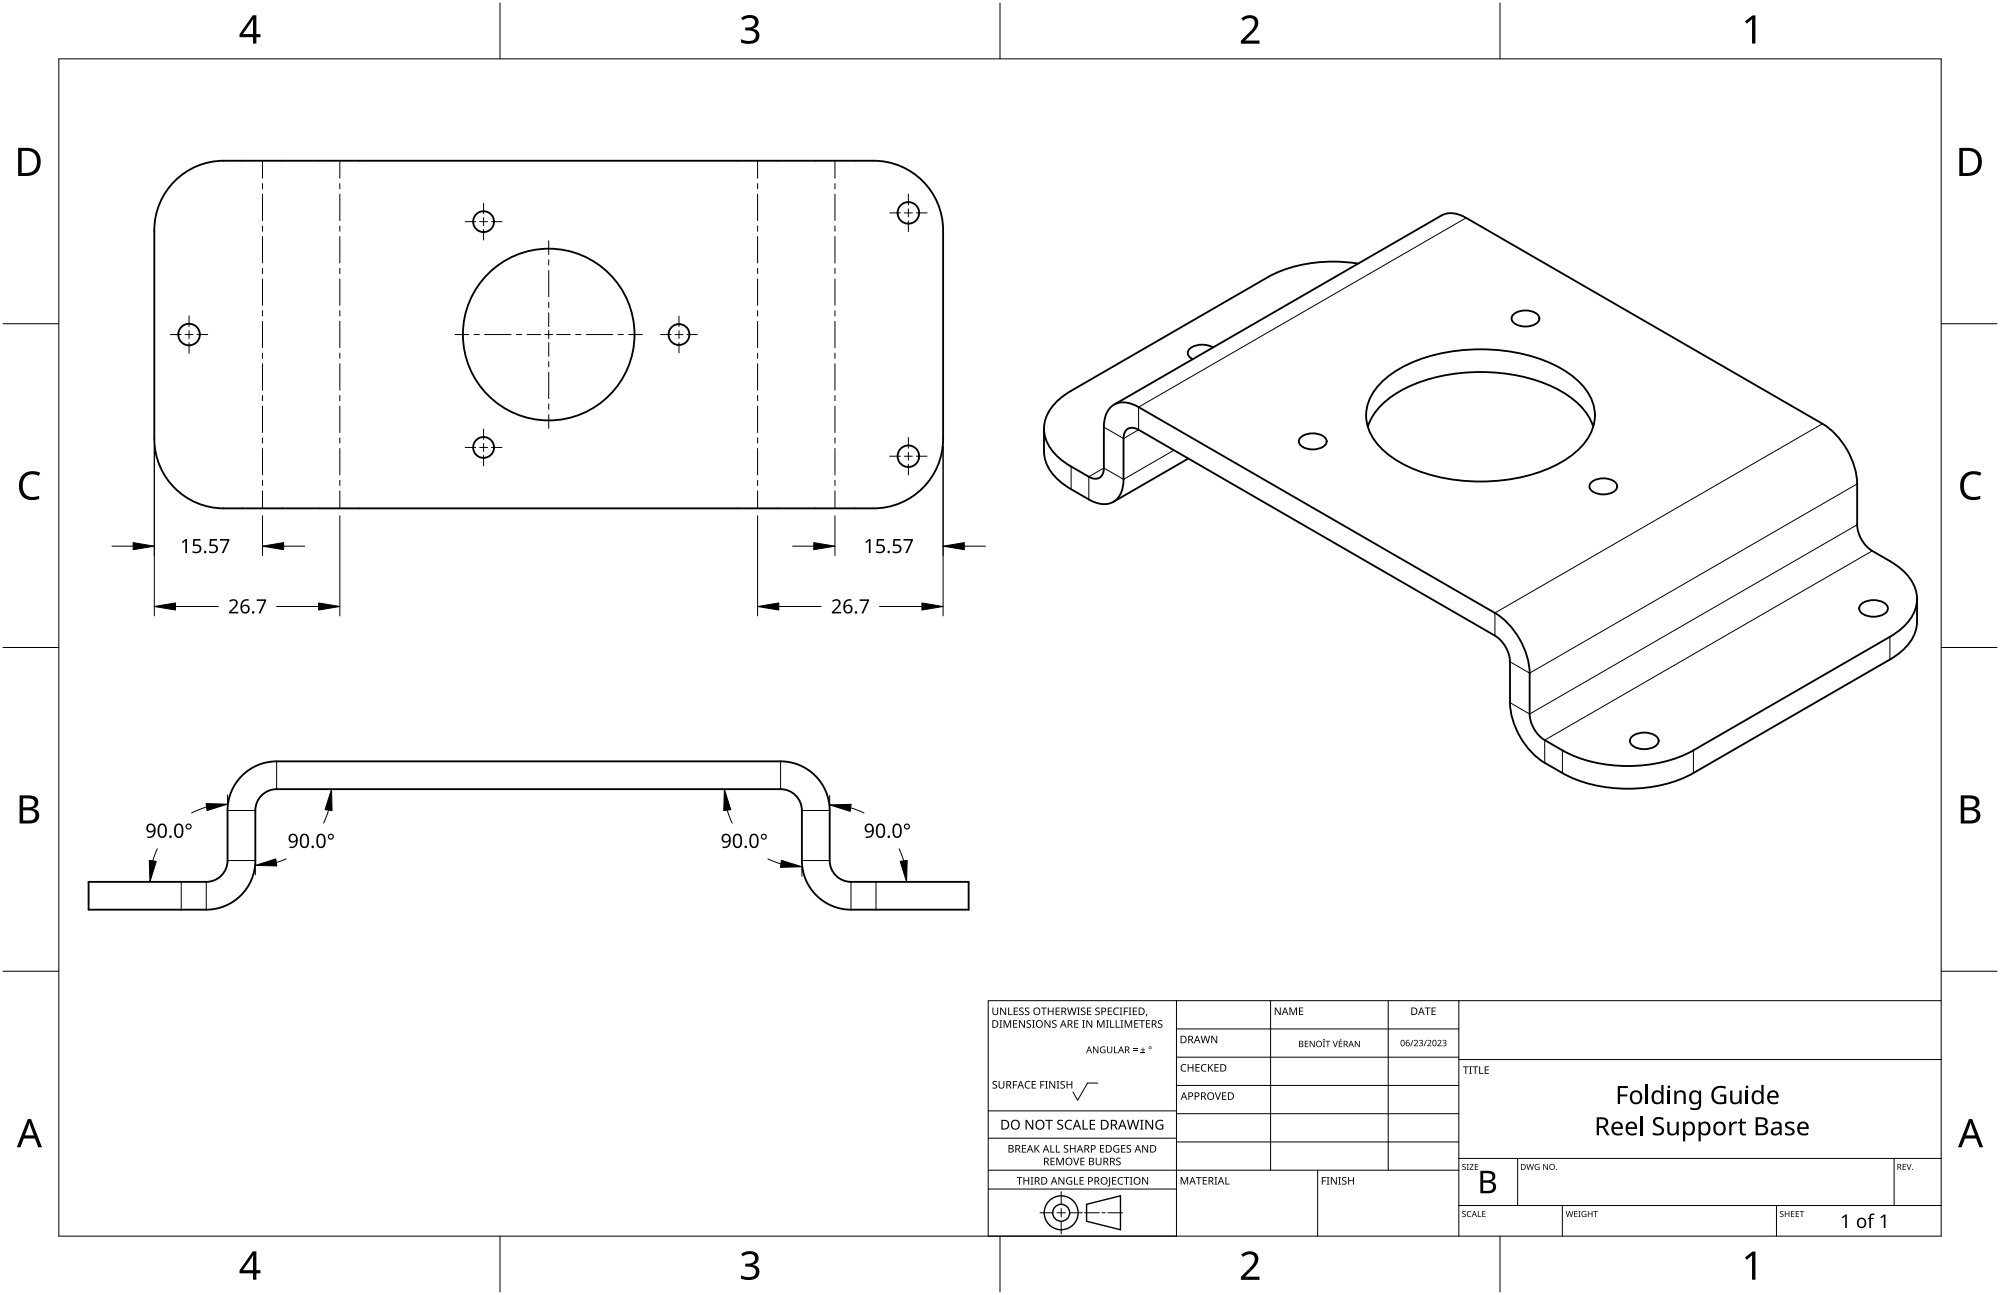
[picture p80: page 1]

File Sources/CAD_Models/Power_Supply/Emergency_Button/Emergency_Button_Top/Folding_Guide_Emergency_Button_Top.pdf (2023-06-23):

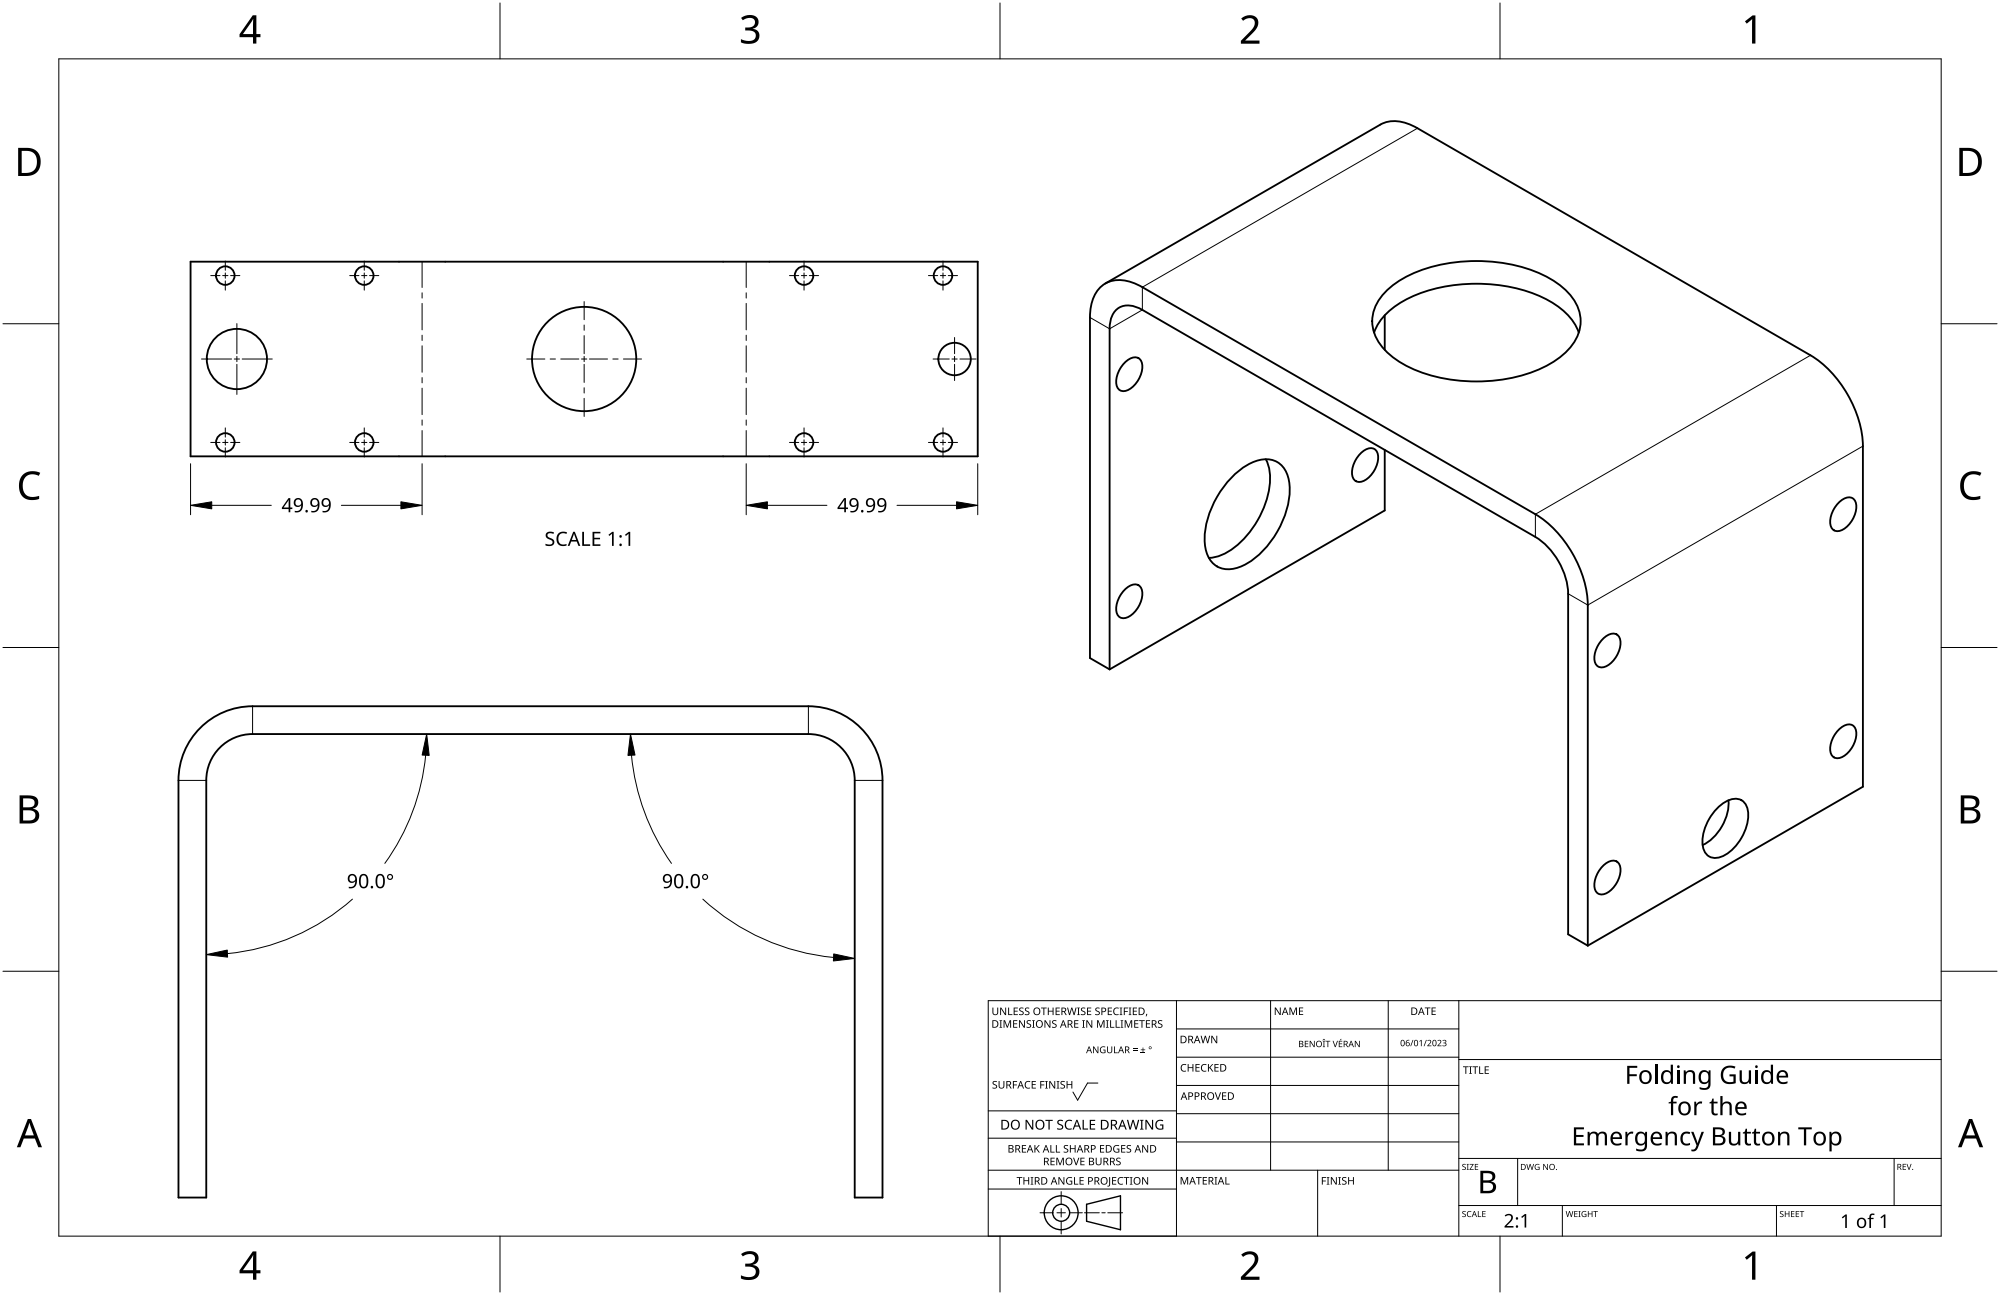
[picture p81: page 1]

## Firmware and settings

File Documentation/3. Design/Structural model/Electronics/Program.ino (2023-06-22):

#include <AccelStepper.h> // library to control the steppers
#include <LiquidCrystal_I2C.h> // Library to control the screen

LiquidCrystal_I2C lcd(0x27, 16, 2); // Define the screen size

// Distribution stepper
int dir_pin = 4 ;
int step_pin = 3 ;

// Cutting stepper
int dir_pin2 = 6 ;
int step_pin2 = 7 ;

// set the pins to read the inputs of the joystick
int VRx = A0;
int VRy = A1;
int btn_dem = 9;

// Variables to read joystick values
int xPosition = 0;
int yPosition = 0;
int mapX = 0;
int mapY = 0;

// Led pins
const int led_Vert = 12 ;
const int led_Red = 10 ;
const int led_Jaune = 11 ;

// Wire detection pin
const int btn_cable = 2;

const int step_per_rev1 = 3200; // number of steps per revolution, here we multiply by 16
const int step_per_rev2 = 3200; // number of steps per revolution, here we multiply by 16

int dem; // variable to register the state of the joystick button
int menu = 0; // variable to navigate between menus
int urgence = false; //variable to signal a problem when it's 1

int position_came = 0; // Variable to controle the position of the stepper when setting the blade for stripping
int position_denude = 0; // variable to save the stripping position of the stepper
int distance_denude = 7; // define the length of wire to expose on both side of the jumper, here 8 mm
int longueur_cable = 3; // variable for the length of sheath to leave on the wire, proportional to the number of pins it would cover on a breadboard
int nbr_jumper = 1; // define the number of jumpers to cut, initialized to 1

//define the steppers with the accel stepper library
AccelStepper stepper1(1, step_pin, dir_pin);
AccelStepper stepper2(1, step_pin2, dir_pin2);

void setup(){
  lcd.init(); // initialize the screen
  pinMode(VRx, INPUT);
  pinMode(VRy, INPUT);
  pinMode(btn_dem, INPUT_PULLUP);
  
  pinMode(led_Vert, OUTPUT);
  pinMode(led_Red, OUTPUT);
  pinMode(led_Jaune, OUTPUT);
  digitalWrite(led_Vert, LOW);
  digitalWrite(led_Red, LOW);
  digitalWrite(led_Jaune, LOW);

  pinMode(btn_cable, INPUT_PULLUP);
  
  Serial.begin(9600) ;

  stepper1.setMaxSpeed(7000); //SPEED = Steps / seconde
  stepper1.setAcceleration(6000); //ACCELERATION = Steps / seconde^2
  stepper1.setCurrentPosition(0);
  
  stepper2.setMaxSpeed(2000);
  stepper2.setAcceleration(6000);
  stepper2.setCurrentPosition(0);
  }

void loop(){
  lcd.backlight();
  cable_detect();

  if (urgence == true){
    digitalWrite(led_Red, HIGH); // the ssystem has an issue with the wire
    digitalWrite(led_Vert,LOW);
    digitalWrite(led_Jaune,LOW);

    lcd.setCursor(0,0);
    lcd.print("No wire         ");
    lcd.setCursor(0,1);
    lcd.print("           ");
  }
  
  else{
    digitalWrite(led_Red, LOW); // the system has no issue with the wire
    digitalWrite(led_Vert,HIGH); // the system works, but no program runs, we light the green LED
    digitalWrite(led_Jaune,LOW); // the yellow LED will light when executing a program running at least one of the steppers
    
    dem = false;
    button_detect();
    get_position_joystick();
    change_menu();
    enter_menu();
  }
}

void cable_detect(){      // Check the presence of wire
  if (digitalRead(btn_cable) == HIGH){
    urgence = true;
  }
  else{
    urgence = false;
  }
}

void button_detect(){
  if (digitalRead(btn_dem) == LOW){     // read the pullup of the joystick's button
    dem = not(dem);
  }
  delay(150);
}

void get_position_joystick(){     // get cordinates of the joystick and map them around zero
  xPosition = analogRead(VRx);
  yPosition = analogRead(VRy);
  mapX = map(xPosition, 0, 1023, -512, 512);   // Map the values of the joystick around 0
  mapY = map(yPosition, 0, 1023, -512, 512);
}

void change_menu(){                         // change the menu with the x coordinates of the joystick
  if ((mapX>=100)&&(mapY>=-175)&& (mapY<=175)){
    if (menu <= 4){
      menu += 1;
      if (menu == 5){
        menu = 0;
      }
    }
  }
  
  if ((mapX<=-100)&&(mapY>=-175)&& (mapY<=175)){
    if (menu >= 0){
      menu -= 1;
      if (menu == -1){
        menu = 4;
      }
    }
  }
  
  delay(150);
}

void enter_menu(){          // will execute the functions of a menu if the user pressed the button of the joystick
  // Menu 0: feed some wire if executed
  if (menu == 0){
    lcd.setCursor(0,0);
    lcd.print("Push wire       ");
    lcd.setCursor(0,1);
    lcd.print("           ");
    
    if (dem){
      lcd.setCursor(0,1);
      lcd.print("Executing       ");
      digitalWrite(led_Jaune,HIGH);
      digitalWrite(led_Vert,LOW);
      distribution(110);
    }
  }

  // Menu 1: Change the number of jumper we want
  if (menu == 1){
    lcd.setCursor(0,0);
    lcd.print("Nbr Jumper:  OUT");
    lcd.setCursor(0,1);
    lcd.print(nbr_jumper);
    lcd.setCursor(String(nbr_jumper).length(),1);
    lcd.print("     ");
    if (dem){
      define_jumper_nbr();
    }
  }

  // Menu 2: Change the length of the jumpers we want
  if (menu == 2){
    lcd.setCursor(0,0);
    lcd.print("Len  Jumper: OUT");
    lcd.setCursor(0,1);
    lcd.print(longueur_cable + 2);
    lcd.setCursor(String(longueur_cable + 2).length(),1);
    lcd.print("     ");
    if (dem){
      define_jumper_long();
    }
  }

  // Menu 3: will set the position of the blade for stripping
  if (menu == 3){
    lcd.setCursor(0,0);
    lcd.print("Set denude:  OUT");
    lcd.setCursor(0,1);
    lcd.print(position_denude);
    lcd.setCursor(String(position_denude).length(),1);
    lcd.print("     ");
    if (dem){
      digitalWrite(led_Jaune,HIGH);
      digitalWrite(led_Vert,LOW);
      define_denude();
    }
  }

  // Menu 4: Cut the jumpers if executed
  if (menu == 4){
    lcd.setCursor(0,0);
    lcd.print("Program         ");
    lcd.setCursor(0,1);
    lcd.print("             ");
    if (dem){
      digitalWrite(led_Jaune,HIGH);
      digitalWrite(led_Vert,LOW);
      lcd.setCursor(0,0);
      lcd.print("Cutting jumper: ");

      // To show the numbers of jumper to cut
      lcd.setCursor(0,1);
      lcd.print("1 over ");
      lcd.setCursor(7,1);
      lcd.print(nbr_jumper);
      
      programme_jumper(nbr_jumper);
      dem = not(dem);
    }
  }
} 

void distribution(float distance){  // feed cable with a given distance in mm
  stepper1.moveTo(step_per_rev1 * distance / (10.3 * 3.14159265)); // 12.24 is the value mesured of the diameter from the extruder
  stepper1.runToPosition();
  stepper1.setCurrentPosition(0);
  delay(100);
}

void coupe(){
  stepper2.moveTo(step_per_rev2); // make a complete turn of the motor to cut
  stepper2.runToPosition();
  stepper2.setCurrentPosition(0);
  delay(100);
}

void define_jumper_nbr(){  // while there's no press of the button we can change the values with y coordinates of the joystick
  while (dem){ //
    get_position_joystick();
    change_nbr_jumper();  // change the value of nbr_jumper
    button_detect();
  }
  delay(100);
}

void change_nbr_jumper(){  // read the joystick coordinates to change the number of jumper
  
  if ((nbr_jumper < 500) && (mapY>=20)){
    if (mapY>= 470){      // add one jumper at the time if the joystick is lean to the extreme
      nbr_jumper += 10;
    }
    else{              // add one jumper at the time if the joystick is lean lightly
      nbr_jumper += 1;
    }
  }
  if (nbr_jumper > 500){   // Jumper high limit
    nbr_jumper = 500;
  }
  
  if ((nbr_jumper > 1) && (mapY<=-20)){  // same as before but suppress jumpers
    if (mapY <=-470){
      nbr_jumper -= 10;
    }
    else{
      nbr_jumper -= 1;
    }
  }
  if (nbr_jumper < 1){  // Jumper low limit
    nbr_jumper = 1;
  }
  
  lcd.setCursor(0,0);
  lcd.print("Nbr Jumper:   IN");
  lcd.setCursor(0,1);
  lcd.print(nbr_jumper);
  lcd.setCursor(String(nbr_jumper).length(),1); // add spaces to avoid flickering on the screen
  lcd.print("     ");
  delay(100);
}

void define_jumper_long(){
  while (dem){    // while there's no press of the button we can change the values with y coordinates of the joystick
    get_position_joystick();
    change_long_jumper();  // change the value of longueur_cable
    button_detect();
  }
  delay(100);
}

void change_long_jumper(){
  if ((mapY>=100) && (longueur_cable < 15)){  // add jumpers if the value is under the limit
    longueur_cable += 1;
  }
  if ((longueur_cable > 1) && (mapY<=-100)){  // remove jumpers if the value is above the limit
    longueur_cable -= 1;
  }
  lcd.setCursor(0,0);
  lcd.print("Len Jumper:   IN");
  lcd.setCursor(0,1);
  lcd.print(longueur_cable + 2);
  lcd.setCursor(String(longueur_cable + 2).length(),1); // spaces to avoid flickering
  lcd.print("     ");
  delay(100);
}

void define_denude(){
  lcd.setCursor(0,0);
  lcd.print("Set denude:   IN");
  while (dem){        // while there's no press of the button we can change the values with y coordinates of the joystick
    get_position_joystick();
    change_pos_came();      // change the value of position_came
    stepper2.moveTo(position_came);
    stepper2.runToPosition();
    button_detect();
  }
  
  position_denude = position_came; //when the button is pressed we register the value for stripping
  position_came = 0;  // resetting the stepper to initial position
  stepper2.moveTo(position_came);
  stepper2.runToPosition(); // then we set the came back to its initial position
}

void change_pos_came(){
  if (((position_came > 0) || ((position_came <= 0) && (mapY > 0)))&& (abs(mapY)>15)){ // will allow to set the position only in the direction the came turns
    position_came += 0.1 * mapY;   // the more we push the joystick in one way, the more steps it will make the mottor move
  }
  lcd.setCursor(0,1);
  lcd.print(position_came);
  lcd.setCursor(String(position_came).length(),1); // spaces to avoid flickering
  lcd.print("     ");
  delayMicroseconds(100);
}

void denude(int pattes){

  stepper2.moveTo(position_denude);  // move the stepper to the position to cut the sheath
  stepper2.runToPosition();

  stepper2.moveTo(position_denude-160); // step back to retain the sheath but not bite into the core
  stepper2.runToPosition();
  delayMicroseconds(1000);
  
  if (pattes == 2){
    distribution(-distance_denude * pattes - 10); // pull the sheath whether we pull it completly, thus the steps added (pattes = 2) or we are centering it (pattes = 1)
  }
  else{
    distribution(-distance_denude * pattes);
  }
  delayMicroseconds(1000);
  
  stepper2.moveTo(-2); // come back to initial position + some offset to compensate an error
  stepper2.runToPosition();
  delay(100);
}

void programme_jumper(int nbr_jumper){
  coupe(); // cut the tip of the wire to ensure to cut the first one to the good length
  
  for (int i=0; i <= nbr_jumper-1; i++){
    
    cable_detect(); // run the program only if the machine has wire
    if (urgence == true){
      menu = 0;
      break;
    }

    lcd.setCursor(0,1);
    lcd.print(i+1);
    lcd.setCursor(String(i+1).length(), 1);
    lcd.print(" over ");
    lcd.setCursor(String(i+1).length() + 6, 1);
    lcd.print(nbr_jumper);
    
    distribution(distance_denude * 2); // feed the wire the double the length to strip
    denude(2); // strip the double lentgh defined before
    distribution(distance_denude * 2 + longueur_cable * 2.54 + 10); // feed the cable to the end of the jumper
    denude(1); // centers the sheath
    distribution(distance_denude); // feed the cable to the end of the jumper + some offset so that there no sheath left on the jumper
    coupe();   // cut a jumper
    delay(100);
  }
  
  lcd.setCursor(0,1);
  lcd.print("            "); // reset the second line when over
}

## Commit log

2023-05-02 Create CAD Files
2023-06-22 Update Program.ino
    modification line 34 about a mistake in the commentary
    [Program.ino]
